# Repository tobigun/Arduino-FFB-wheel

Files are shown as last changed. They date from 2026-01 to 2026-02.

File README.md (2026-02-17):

# Customized Arduino-FFB-wheel for Guillemot Force Feedback Racing Wheel
## About this project
### Motivation
It gets more and more difficult to find working Windows 11 drivers for this wheel.

Even the old [Vista drivers](https://support.thrustmaster.com/en/product/ffdrw-en/) which worked fine for me some years ago only work with the iRacing FFB test program (WheelCheck.exe) anymore, but not with any of my games - they simply crash. I already replaced "System32/immpid.dll" with the one from "SysWOW64" and although this fixes the crashes I do not get any Force Feedback effects in games at all (the green effect LED on the Main PCB also does not blink).

There is also another old [driver on archive.org](https://archive.org/details/Guillemot-Thrustmaster-ForceFeedback-wheel-64bit-driver) which is supposed to work according to some forums. But even after disabling the Windows driver signature check the driver was marked as non-functional in the device manager and was not functional.

As a consequence I decided to reverse engineer the hardware and replace the Main PCB of the wheel with an Arduino Pro Micro board. This way it supports Force Feedback via USB HID and does not need any drivers at all.
The nice thing about this wheel is that the Motor Control PCB can be reused and only the Logic Board has to be replaced.

For the firmware I tried multiple projects, e.g.:
- [ranenbg/Arduino-FFB-wheel](https://github.com/ranenbg/Arduino-FFB-wheel)
- [vsulako/AFFBWheel](https://github.com/vsulako/AFFBWheel) (see my [unfinished fork here](https://github.com/tobigun/AFFBWheel))
- [YukMingLaw/ArduinoJoystickWithFFBLibrary](https://github.com/YukMingLaw/ArduinoJoystickWithFFBLibrary)

Arduino-FFB-wheel was the most complete, so this project was used as the foundation.

### Game Compatibility Matrix
|Game|Store|Status|
|----|----|---|
|Assetto Corsa|Steam|OK
|Assetto Corsa Competizione|Steam|OK
|DiRT Rally 2.0|Steam|OK|
|Forza Horizon 4|Steam|OK. Requires the [Steering Wheel HID Profile](#hid-profiles), otherwise wheel will not be detected.|
|Forza Horizon 5|Steam|OK. Requires the [Generic HID Profile](#hid-profiles), otherwise game will crash at start.|
|NFS Heat|Steam|Only Steering, no FFB effects|
|NFS Hot Pursuit Remastered|Steam|OK|
|NFS Most Wanted|Steam|OK. Seems to support vibrations only, as FFB effects are week.|
|NFS Undercover|Steam|OK|

### Firmware
This repo is a fork of Miloš Ranković's [Arduino-FFB-wheel](https://github.com/ranenbg/Arduino-FFB-wheel), customized for the Guillemot Force Feedback Racing Wheel. As none of the pre-compiled binaries of the original project were suitable for this wheel, this project provides a configuration for the hardware and some minor software adjustments.

**Hardware configuration:**
- Analog X-Axis
- Hat Switch
- PWM motor control in 0-50-100 mode (hardcoded, so no need to configure it via the config software)
- Matrix keypad with 12 buttons
- Usage of 5 analog axis:
  - X-Axis (wheel angle)
  - Throttle
  - Brake
  - 2x analog levers on the wheel
- Force Feedback (of course)

### Original PCBs
The wheel consists of five PCBs:

- Main PCB, i.e. the logic board with the I-Force 2.0 chip:<br>
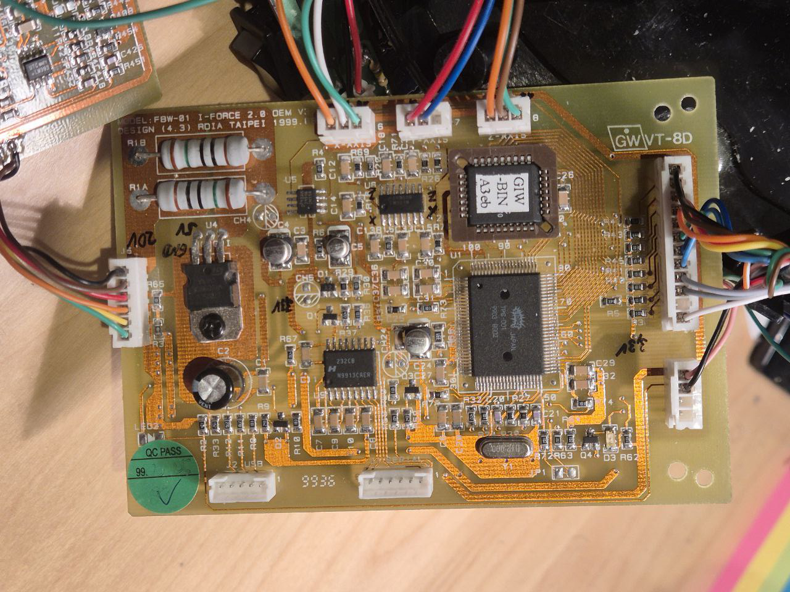
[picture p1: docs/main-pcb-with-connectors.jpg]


- Motor PCB (contains the PWM H-Bridge):<br>
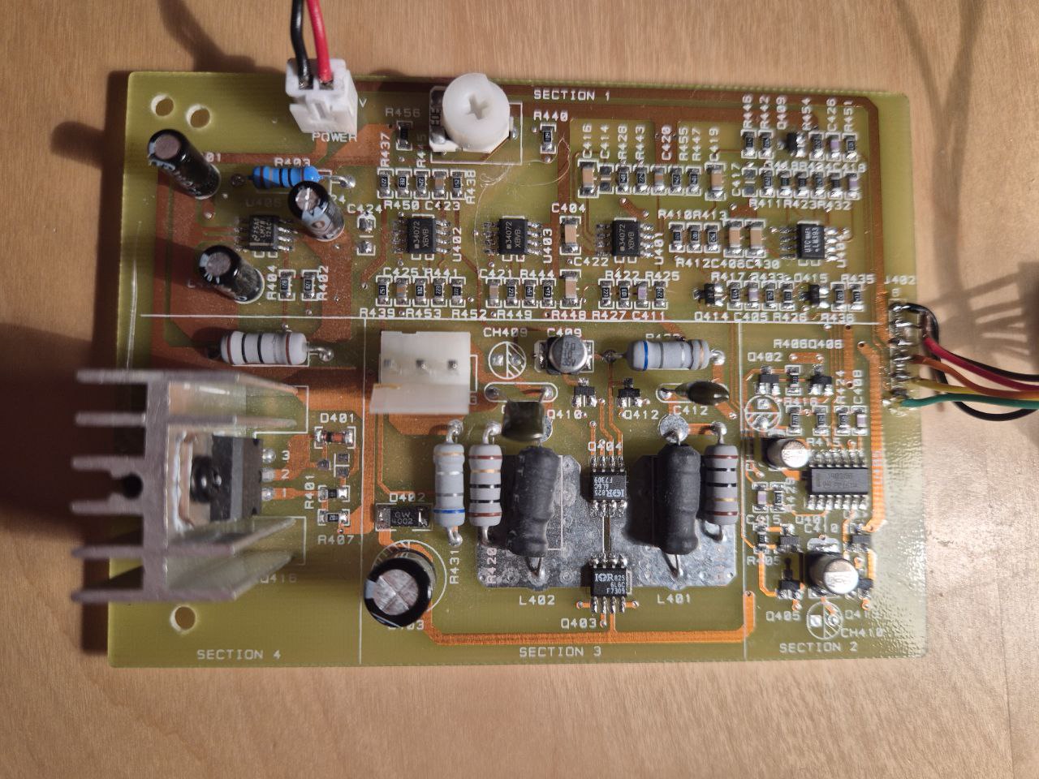
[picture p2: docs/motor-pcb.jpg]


- Front Button PCB:<br>
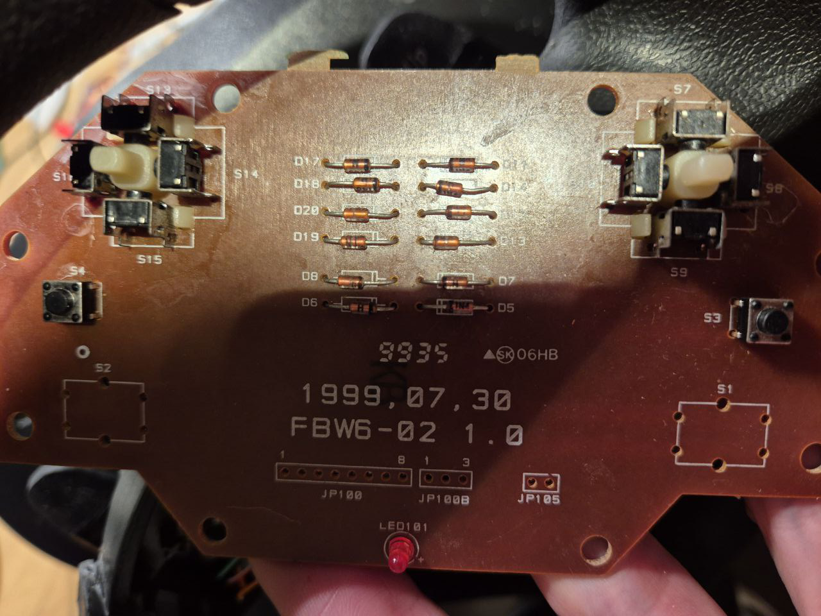
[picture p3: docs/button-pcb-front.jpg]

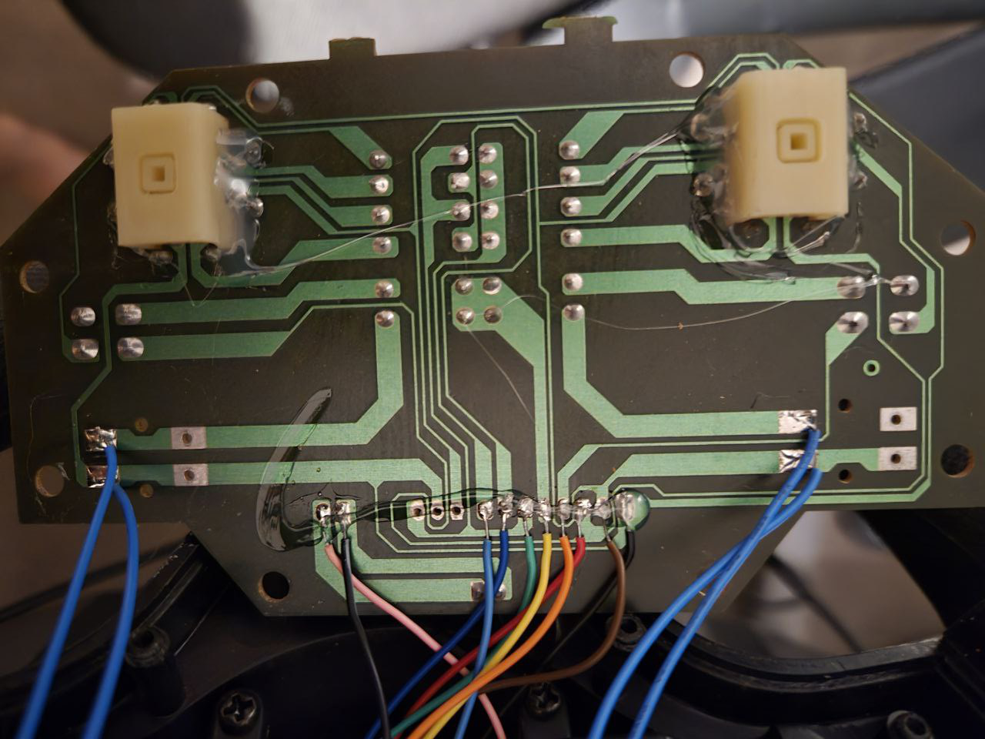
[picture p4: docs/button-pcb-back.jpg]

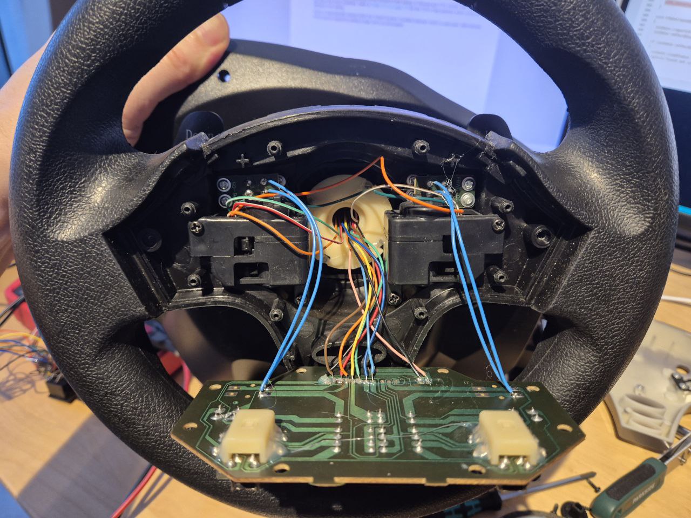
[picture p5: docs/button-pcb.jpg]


- Gear Shift PCB:<br>
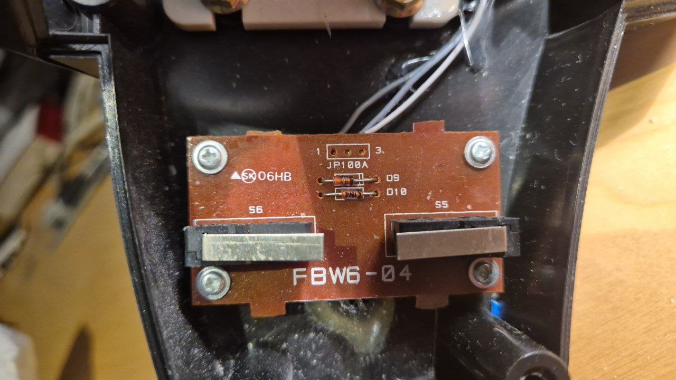
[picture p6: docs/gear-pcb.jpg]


- Power PCB (Note: already modified on the pictures). Contains power connector and switch, pedal connector and a digital switch (74HC4066). The 74HC4066 disables the two analog levers on the wheel when the pedals are connected.<br>
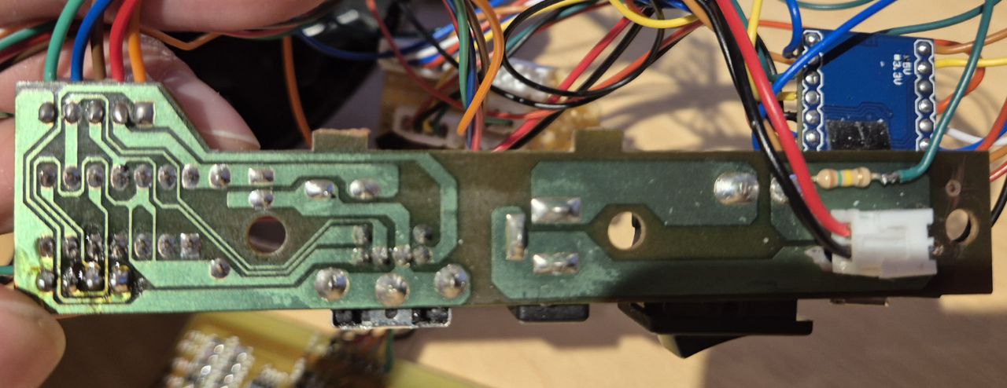
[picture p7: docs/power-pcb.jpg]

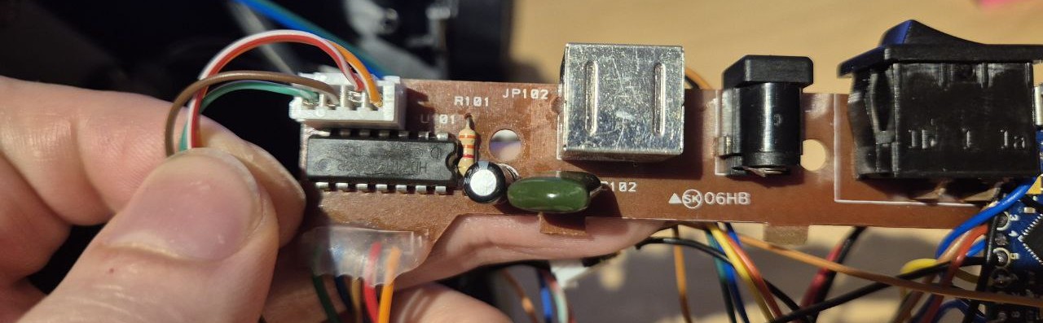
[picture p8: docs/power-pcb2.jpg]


All PCBs connected:
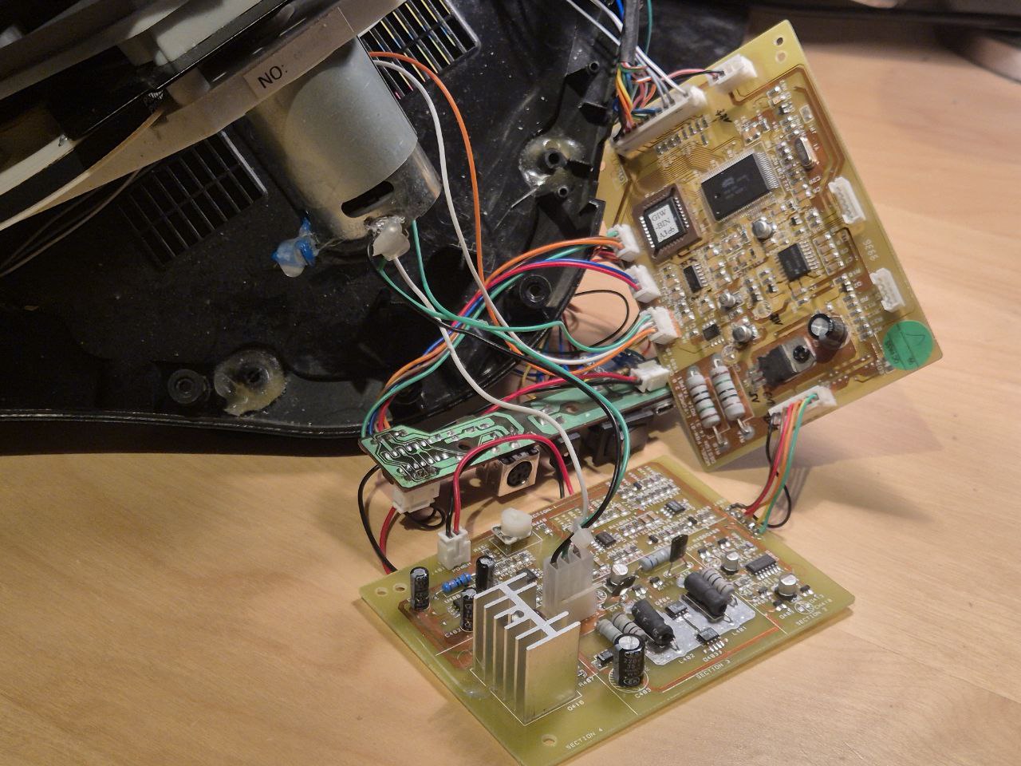
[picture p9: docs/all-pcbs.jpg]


### Arduino Main PCB
All of the original PCBs will be reused. The only PCB that will be replaced is the Main PCB. Instead an Arduino Pro Micro is used. I placed it on the Power PCB:
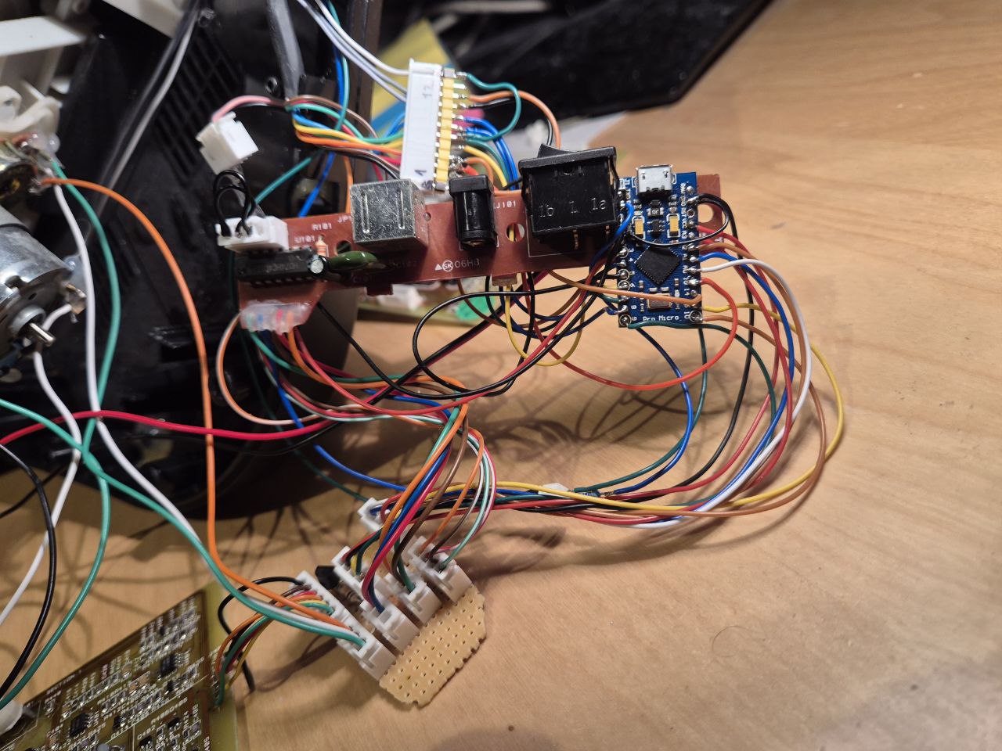
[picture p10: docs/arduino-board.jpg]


#### Wiring
Here is the overview of the connectors that are located on the Main PCB that now have to be connected to the Arduino board instead:
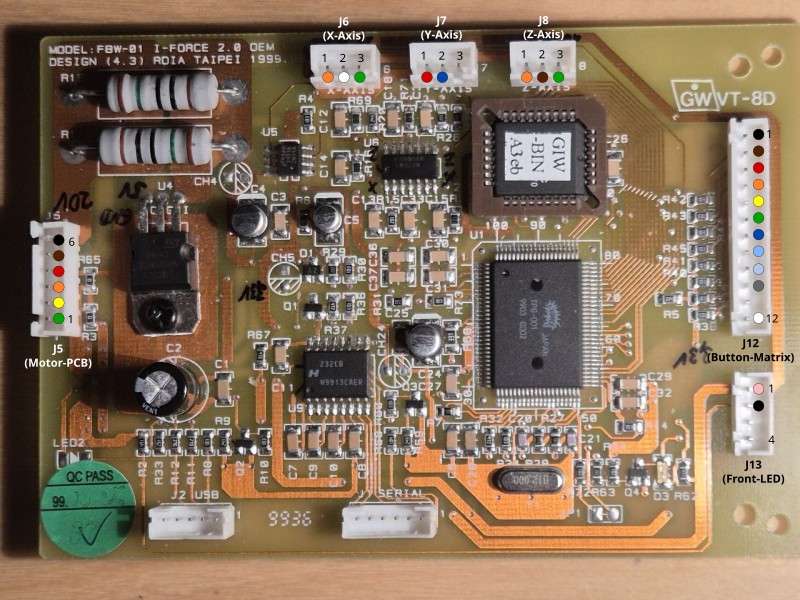
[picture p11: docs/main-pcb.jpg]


<table>
<tr><th colspan="3">Connector</th><th rowspan="2">Signal</th><th rowspan="2">Pin (ESP32-S3)</th><th rowspan="2">Pin (Pro Micro)</th><th rowspan="2">Comment</th></tr>
<tr><th>Name</th><th>Pin</th><th>Color</th></tr>

<tr><td rowspan="6">J5 (Motor PCB Connector)</td>
    <td>1</td><td style="background:green">green</td><td>Motor PWM</td><td>GP42</td><td>D9</td>
    <td rowspan="6">* Motor Enable switch must be connected to GP39/D10 via a BJT transistor to make sure that the motor is disabled when the microcontroller is powered down (i.e. not connected to USB).<br>
    This is necessary as the Motor PCB would erroneously interpret the missing PWM signal to apply maximum force. It would turn the wheel with full force in one direction and try to move it past the end stop. As this is not possible the motor gets quite hot after some minutes.
    <br>See schematic for more info.
    </td></tr>
<tr><td>2</td><td style="background:yellow">yellow</td><td>Motor Enable switch</td><td>[GP41]*</td><td>[D10]*</td></tr>
<tr><td>3</td><td style="background:orange">orange</td><td>GND</td><td colspan="2">GND</td></tr>
<tr><td>4</td><td style="background:red">red</td><td>GND</td><td colspan="2">GND</td></tr>
<tr><td>5</td><td style="background:brown">brown</td><td>GND</td><td colspan="2">GND</td></tr>
<tr><td>6</td><td style="background:black;color:white">black</td><td>+20V (from power supply)</td><td colspan="2">- (unused)</td></tr>

<tr><td rowspan="3">J6 (X-Axis Potentiometer)</td>
    <td>1</td><td style="background:orange">orange</td><td>VCC</td><td colspan="2">VCC</td><td rowspan="3"></td></tr>
<tr><td>2</td><td style="background:white">white</td><td>Analog X-Axis (0 .. VCC)</td><td>A0</td><td>A0</td></tr>
<tr><td>3</td><td style="background:green">green</td><td>GND</td><td colspan="2">GND</td></tr>

<tr><td rowspan="3">J7 (Y-Axis Potentiometer)</td>
    <td>1</td><td style="background:red">red</td><td>74HC4066 Supply Voltage</td><td colspan="2">VCC</td><td rowspan="3"></td></tr>
<tr><td>2</td><td style="background:blue;color:white">blue</td><td>Analog Y-Axis (0 .. VCC)</td><td>A1</td><td>A1</td></tr>
<tr><td>3</td><td style="background: repeating-linear-gradient(45deg,#eee,#eee 4px,#ccc 4px,#ccc 8px);">n.c.</td><td>-</td><td colspan="2">-</td></tr>

<tr><td rowspan="3">J8 (Z-Axis Potentiometer)</td>
    <td>1</td><td style="background:orange">orange</td><td>VCC</td><td colspan="2">VCC</td><td rowspan="3"></td></tr>
<tr><td>2</td><td style="background:brown">brown</td><td>Analog Z-Axis (0 .. VCC)</td><td>A3</td><td>A2</td></tr>
<tr><td>3</td><td style="background:green">green</td><td>GND</td><td colspan="2">GND</td></tr>

<tr><td rowspan="12">J12 (Button Matrix)</td>
    <td>1</td><td style="background:black;color:white">black</td><td>Matrix column 1</td><td>GP38</td><td>D5</td><td rowspan="12"></td></tr>
<tr><td>2</td><td style="background:brown">brown</td><td>Matrix column 2</td><td>GP37</td><td>D14</td></tr>
<tr><td>3</td><td style="background:red">red</td><td>Matrix column 3</td><td>GP36</td><td>D15</td></tr>
<tr><td>4</td><td style="background:orange">orange</td><td>Matrix column 4</td><td>GP35</td><td>D2</td></tr>
<tr><td>5</td><td style="background:yellow">yellow</td><td>Matrix row 1</td><td>GP17</td><td>D6</td></tr>
<tr><td>6</td><td style="background:green">green</td><td>Matrix row 2</td><td>GP33</td><td>D7</td></tr>
<tr><td>7</td><td style="background:blue;color:white">blue</td><td>Matrix row 3</td><td>GP18</td><td>D1 (TX0)</td></tr>
<tr><td>8</td><td style="background:#add8e6">light blue</td><td>Matrix row 4</td><td>GP34</td><td>D4</td></tr>
<tr><td>9</td><td style="background:#d3d3d3">light grey</td><td>Gear Shifter - Up (Matrix column 1)</td><td>GP38</td><td>D5</td></tr>
<tr><td>10</td><td style="background:grey">grey</td><td>Gear Shifter - Down (Matrix column 2)</td><td>GP37</td><td>D14</td></tr>
<tr><td>11</td><td style="background: repeating-linear-gradient(45deg,#eee,#eee 4px,#ccc 4px,#ccc 8px);">n.c.</td><td>-</td><td colspan="2">-</td></tr>
<tr><td>12</td><td style="background:white">white</td><td>Gear Shifter - Matrix row (Matrix row 2)</td><td>GP33</td><td>D7</td></tr>

<tr><td rowspan="4">J13 (Front LED)</td>
    <td>1</td><td style="background:#ff66cc">rose</td><td>LED Anode (+)</td><td>[GP40]*</td><td>[D3]*</td><td rowspan="4">* Connect LED's Anode via 820 Ohms resistor to pin.<br>See schematic for more info.</td></tr>
<tr><td>2</td><td style="background:black;color:white">black</td><td>LED Cathode (-)</td><td colspan="2">GND</td></tr>
<tr><td>3</td><td style="background: repeating-linear-gradient(45deg,#eee,#eee 4px,#ccc 4px,#ccc 8px);">n.c.</td><td>-</td><td colspan="2">-</td></tr>
<tr><td>4</td><td style="background: repeating-linear-gradient(45deg,#eee,#eee 4px,#ccc 4px,#ccc 8px);">n.c.</td><td>-</td><td colspan="2">-</td></tr>

<tr><td rowspan="4">JP101 (Analog Levers)<br>[Optional]</td>
    <td>1</td><td style="background:orange">orange</td><td>VCC</td><td colspan="2">VCC</td>
    <td rowspan="4">Wires can be unsoldered from connector JP101 of the power PCB and directly connected to the microcontroller.
    This way the pedals and levers can be used in parallel (5 instead of 3 axes). The Pins 2+3 on the JP101 connector on the power board should be pulled high then (i.e. connected to Pin 1).<br>See schematic for more info.</td></tr>
<tr><td>2</td><td style="background:red">red</td><td>Analog Axis - Lever left</td><td>A4</td><td>A3</td></tr>
<tr><td>3</td><td style="background:brown">brown</td><td>Analog Axis - Lever right</td><td>A5</td><td>A8</td></tr>
<tr><td>4</td><td style="background:green">green</td><td>GND</td><td colspan="2">GND</td></tr>

<tr><td rowspan="2">Blue Front LED<br>[Optional]</td>
    <td>A</td><td style="background:blue"></td><td>LED Anode (+)</td><td>[GP39]*</td><td>[D0]* (RX1)</td>
    <td rowspan="2">* Connect LED's Anode via 4.7 kOhms resistor to pin.<br>See schematic for more info.</td>
    </tr>
<tr><td>C</td><td style="background:black;color:white"></td><td>LED Cathode (-)</td><td colspan="2">GND</td></tr>

<tr><td rowspan="2">Green Front LED<br>[Optional]</td>
    <td>A</td><td style="background:green"></td><td>LED Anode (+)</td><td colspan="2">[+20V]*</td>
    <td rowspan="2">* Connect LED's Anode via 150 kOhms resistor to +20V.<br>See schematic for more info.</td>
    </tr>
<tr><td>C</td><td style="background:black;color:white"></td><td>LED Cathode (-)</td><td colspan="2">GND</td></tr>

<tr><td rowspan="2">Profile Switch<br>[Optional]</td>
    <td>1</td><td></td><td>Pin 1</td><td>GP7</td><td>D16</td>
    <td rowspan="2">For three pin switches: connect middle pin to D16 and any of the other two pins to GND.<br>
    </td></tr>
<tr><td>2</td><td style="background:black;color:white"></td><td>Pin 2</td><td colspan="2">GND</td></tr>
</table>

Make a little connector hub PCB to hold the motor switch transistor and  to connect all of the GND and VCC pins together. This way you can keep the existing connectors and you will still be able to reconnect them to the original Main PCB. But you can also cut the original connectors and solder the wires directly to the Arduino board.
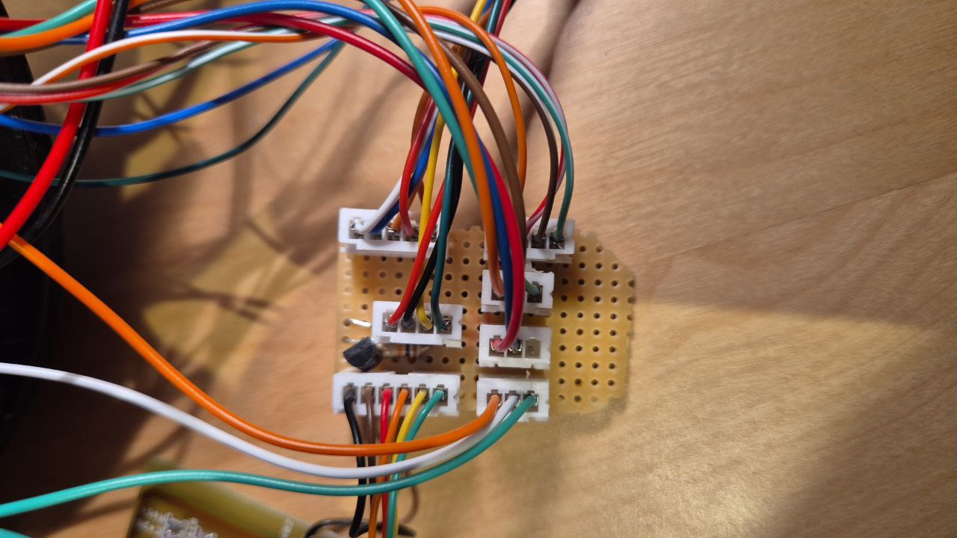
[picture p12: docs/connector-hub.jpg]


#### HID Profiles
A Profile Switch can be added to select between to HID profiles:
- Switch open: Generic Joystick with generic X/Y/Z/Rx/Rz Axes (default)
- Switch closed: Steering wheel with Steering/Brake/Accelerator/Rx/Rz Axes

Switching profiles is necessary as there is no unified way to detect a Driving Wheel on Windows.
- Some games only detect a driving wheel if a Steering-Wheel Axis is present in the USB HID descriptor (e.g. Forza Horizon 4).
  - It seems that mostly older DirectInput based games require this profile as DirectInput uses a heuristic to detect wheels based on the axes of the controller ([see Wine DirectInput Port](https://github.com/wine-mirror/wine/blob/master/dlls/dinput/joystick_hid.c)).
- Some games require a generic X-Axis and do not work (or crash) when a Steering-Wheel Axis is present.
  - For example, Forza Horizons 5 crashes if a Steering-Wheel Axis is found.

##### Registry Tweak for Generic Profile
Instead of adding a switch to change the HID profile, for some games (like Forza Horizon 4) the Generic Profile also works if the following Windows registry keys are added via `regedit`:
```
Computer\HKEY_CURRENT_USER\System\CurrentControlSet\Control\MediaProperties\PrivateProperties\Joystick\OEM\VID_1B4F&PID_9206
Computer\HKEY_LOCAL_MACHINE\System\CurrentControlSet\Control\MediaProperties\PrivateProperties\Joystick\OEM\VID_1B4F&PID_9206
```
Add or modify the following value/data pair in these keys:
|Name|Type|Data
|----|----|----
|OEMData|REG_BINARY|43 00 88 01 fe 00 00 00

This can be achieved by double clicking on the `FFB_misc_programs/wheel-oemdata-add.reg` file.
The entries can be removed again with the `wheel-oemdata-remove.reg` file.

The bits of OEMData are described [here](https://sourceforge.net/p/timidity/git/ci/master/tree/windrv/mmddk.h#l230) but do not seem to be that important, as long as it starts with `43`.

See [Steam Community article on Forza Horizon 4 by LeadMagnet](https://steamcommunity.com/sharedfiles/filedetails/?id=2909923087) for more info.

> [!IMPORTANT]
> Make sure that the registry entries are removed again for Forza Horizons 5, as this game crahes if the entries are present.

------------------

# Arduino-FFB-wheel
A stand-alone DirectInput USB device is recognized in Windows as a joystick with force feedback functionality, based on BRWheel by Fernando Igor in 2017.

Firmware features:
- supported Arduino boards: Leonardo, Micro, and ProMicro (ATmega32U4, 5V, 16MHz)
- 4 analog axis + 1 for an optical or magnetic encoder, 2 FFB axis (with multichannel PWM or DAC output)
- for 2 FFB axis mode - 2 magnetic encoders may be used (for X and Y axis)
- automatic or manual analog axis calibration
- up to 16 buttons by 4x4 matrix or via **[button box firmware](https://github.com/ranenbg/Arduino-FFB-wheel/tree/master/tx_rw_ferrari_458_wheel_emu_16buttons)** uploaded to Arduino Nano/Uno
- up to 24 buttons by 3x8bit shift register chips
- analog XY H-pattern shifter (configurable to 6 or 8 gears + reverse gear, XY axis invert, reverse gear button invert)
- fully supported 16bit FFB effects (custom force effect not implemented)
- envelope and conditional block effects, start delay, duration, deadband, and direction enable
- FFB calculation and axis/button update rate 500Hz (2ms period)
- many firmware options (external 12bit ADC/DAC, automatic/manual pedal calibration, z-index support/offset/reset, hat switch, button matrix, external shift register, hardware wheel re-center, xy analog H shifter, FFB on analog axis)
- RS232 serial interface for configuring many firmware settings (10ms period)
- fully adjustable FFB output in the form of 4-channel digital 16bit PWM or 2-channel analog 12bit DAC signals
- available PWM modes: PWM+-, PWM+dir, PWM0-50-100, RCM (if 2 FFB axis: 2CH PWM+-, 2CH PWM+dir, 2CH PWM0-50-100, 2CH RCM)
- available DAC modes: DAC+-, DAC+dir, DAC0-50-100 (if 2 FFB axis: 1CH DAC+-, 2CH DAC+dir, 2CH DAC0-50-100)
- load cell support for 24bit HX711 chip (for Y axis only)
- all firmware settings are stored in EEPROM (and automatically loaded at each Arduino powerup)
- original wheel control user interface **[Arduino FFB gui](https://github.com/ranenbg/Arduino-FFB-gui)** for an easy configuration and monitoring of all inputs/outputs 

Detailed documentation and more information about the firmware can be found in txt files inside the `docs/fw` folder.

# Firmware pinouts and wiring diagrams
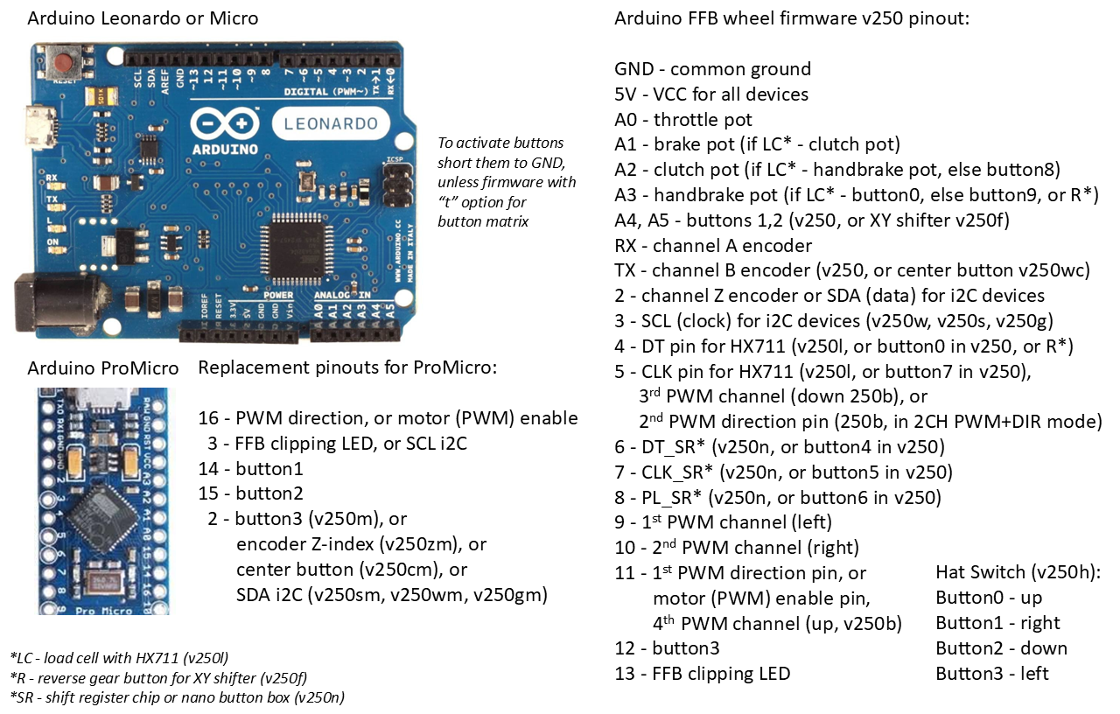
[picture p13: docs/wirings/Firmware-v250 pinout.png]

**Note:** some pin mappings in the image are outdated. Check the wiring table above for the correct ones.
## Optical encoder and LED wiring
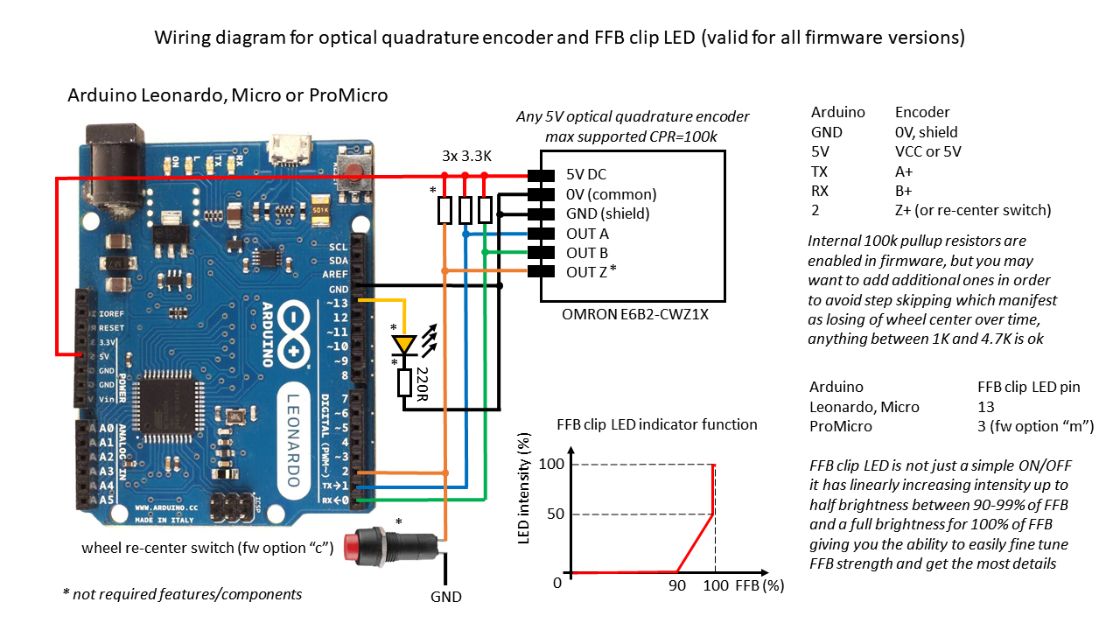
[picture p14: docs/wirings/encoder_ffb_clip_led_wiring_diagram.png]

## Button matrix pinouts
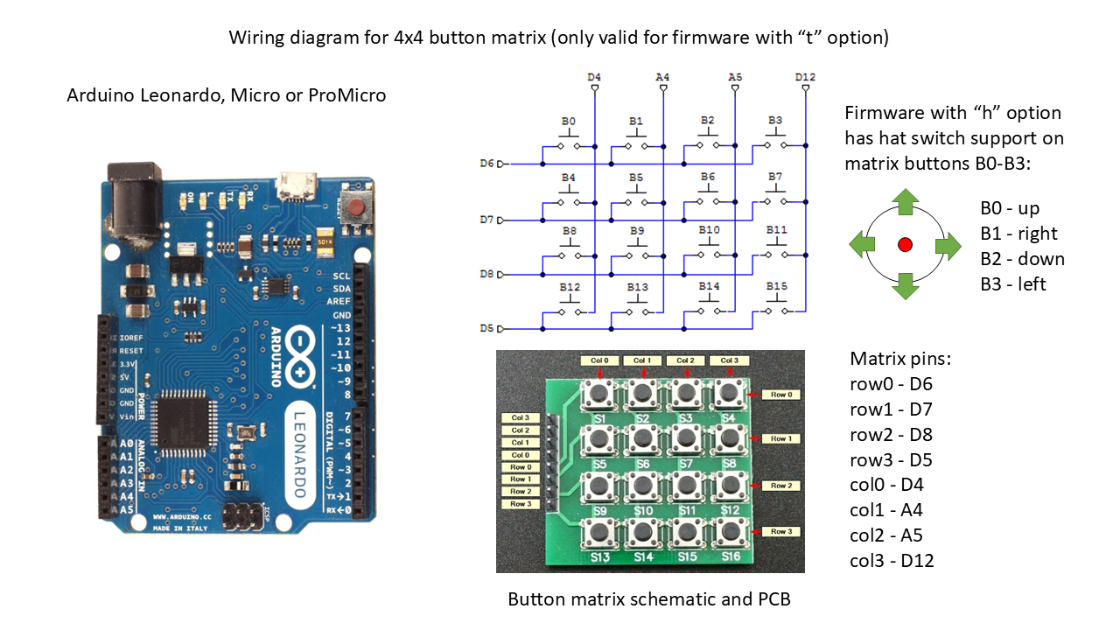
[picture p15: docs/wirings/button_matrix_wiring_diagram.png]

**Note:** the digital inputs for the matrix are not correct in the image. Check the wiring table above for the correct ones.

## Firmware upload procedure
You can use XLoader from the `misc_programs/XLoader` folder:
- set 57600baud, ATmega32U4 microcontroller and select desired HEX
- press the reset button on Arduino (or shortly connect the RST pin to GND)
- select the newly appeared COM port (Arduino in bootloader mode*) and press upload, you will only have a few seconds

*It is possible that some cheap Chinese clones of Arduino Leonardo, Micro, or ProMicro do not have a bootloader programmed. In that case you need to upload the original Arduino Leonardo bootloader first. You can find more details about it here: https://docs.arduino.cc/built-in-examples/arduino-isp/ArduinoISP

## How to compile the source
In order to compile the firmware yourself you may use Windows 11, you need to install Arduino IDE v2.3.6 and Arduino Boards v1.8.7. You must place the libraries (from the `libraries` folder) in your `.../documents/Arduino/Libraries` folder.

## Credits
- Miloš Ranković: [Arduino-FFB-wheel](https://github.com/ranenbg/Arduino-FFB-wheel)
- FFB HID and USB core for Arduino by: Peter Barrett
- BRWheel firmware by: Tero Loimuneva, Saku Kekkonen, Etienne Saint-Paul, and Fernando Igor
https://github.com/fernandoigor/BRWheel/tree/alphatest

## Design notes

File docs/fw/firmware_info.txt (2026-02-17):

Milos Rankovic, ranenbg@gmail.com
first created 21.11.2018.
last updated 02.08.2025.

This txt file contains full details about Arduino FFB wheel firmware capabilities and features:

Supported Arduino boards - Leonardo, Micro or ProMicro (5V, 16MHz clock)

firmware	PWM freq	PWM mode	PWM res		steering	brake		throttle	clutch		handbrake	buttons		HAT Switch	XYshifter

ver250		8KHz*		PWM+-*		2047*		16bit	        16bit(LC,a,s)	12bit(a,s)	12bit(a,s)	12bit(a,s)	24(16)		1		10bit

*fully configurable through RS232 or Wheel control v2.6.5

LC - load cell module HX711 24bit, 1 sample no-averaging, limited by Microsoft FFB driver to 16bits (0-65535)
a - Arduino analog input, 10bit (0-1023)
s - ADS1015, external ADC, 12bit (0-4095)
**HID supports total of 28 buttons, but only 24 buttons are visible, because 4 buttons are reserved for D-pad (HAT switch) 
firmware is compatible with any Thrustmaster wheel rim at 3.3v
be careful! 5V to 3.3V logic level converter is needed from Arduino wheel base board to Thrustmaster wheel rim
first 6 buttons are reserved for recognition of Thrustmaster wheel rims
Leonardo, Micro or ProMicro - up to 8 buttons are available on the main Arduino board (may be less depending on firmware options)
With external Arduino Nano board acting as a button box, up to 16 buttons can be used (button box firmware included in a separate *.ino file)
Only with external 8bit shift register chips 24 buttons can be used (if 3 are stacked together)

Axis readout adjustment (LC, a, s) and auto calibration (on/off) - requires recompiling

Available sensors on X-axis (for steering, tied to FFB axis):
[1] Optical encoder - quadrature readout of two channels, 1k-10k pullup resistors optional, available CPR range in firmware depends on selected deg of rotation (DOR), the limitation is CPR*DOR/360 <= 600k
[2] Magnetic encoder - 12bit i2C AS5600 (default CPR=4096, set to full precision and 2.2ms response time, multiturn detection supported)
[3] Potentiometer - any linear pot 10k-100k Ohm

USB poll. rate	FFB calc. rate	RS232 refresh	RS232 baud rate		axis update rate	LC update rate		buttons,D-pad,XY_shifter update rate

500Hz (2ms)	500Hz (2ms)	100Hz (10ms)	115200bit/s		500Hz (2ms)		80Hz (12.5ms)		500Hz (2ms)

Supported FFB effects: constant force, ramp, spring, damper, inertia, friction, sine, triangle, square, sawtoothup, sawtoothdown

FFB mics: all effects are calculated with 32bit precision and scaled down to 16bit in HID; realistically calculated damper, inertia and friction; fully working periodic effects;
fully implemented condition and envelope block effects, effect duration, start delay, direction for 2 axis FFB, *2channel PWM/DAC output for xFFB and yFFB

*FFB effects that support 2 FFB axis are: constant force, sine and spring

Internal FFB effects: auto centering spring, damper, inertia, friction and end stop spring (can be turned on/off through serial interface)

Firmware features: RS232 interface for adjusting all FFB parameters, LC brake pressure, pedal autocalibration, minimal PWM value, rotation angle, recenter wheel,
recalibrate wheel, recalibrate pedals, wheel version info reporting, turning various desktop effects on/off, turn on/off real-time FFB signal monitor, save FFB config to EEPROM,
adjustment of encoder CPR, fully adjustable PWM settings that are stored in EEPROM, FFB clip LED indicator (lights up gradually from last 10% of FFB signal level),
4x4 button matrix, CPR range up to 100k, wheel angle used as metric for spring, damper, inertia and friction effects, encoder z-index reset, PWM motor enable pin feature, single or double magnetic encoder support, 2 FFB axis and 4 channel PWM or 2 channel DAC output, 3x8bit shift register chip support for 24 buttons

Wheel control GUI: made from scratch in Processing 3.5.4, visualizes all axis and buttons including serial commands sent and received from Arduino, full adjustment of FFB effect gains,
FFB signal monitor graph, load/save last settings from EEPROM, recenter wheel, recalibrate pedals, encoder CPR adjustment, PWM adjustment, COM port CFG via dialog,
Axis colors CFG txt, storing/loading FFB profiles to/from PC, autodetection of firmware version, XY analog shifter support, manual pedal axis calibration, PWM0.50.100 mode, hardware button wheel re-center, RCM PWM mode, Z-index reset button, FFB axis selector, XY shifter advanced config buttons, advanced info startup diagnostics, encoder type indicator, detection of available wheel buttons, 2-axis FFB joystick representation instead of a wheel, new CP5 blue FFB sliders, re-sizeable GUI window, latest version is v2.6.5

FFB output options (requires recompiling):
[1] digital: 4 channel fully configurable PWM settings - PWM frequency (tied to PWM resolution), PWM types (phase correct or fast pwm), 1CH PWM modes (PWM+-, PWM+DIR, PWM0-50-100, RCM), 2CH PWM modes (2CH PWM+-, 2CH PWM+DIR, 2CH PWM0-50-100, 2CH RCM - not used), changes of PWM settings require restarting Arduino
[2] analog: 2 external i2C 12bit MCP4725 DAC's, 1CH DAC modes (DAC+-, DAC+DIR, DAC0-50-100), 2CH DAC modes (1CH DAC+- (xFFB), 2CH DAC+DIR, 2CH DAC0-50-100), changes of DAC settings do not require restarting Arduino

          PWM freq  index: 0,   , 1    , 2    , 3   , 4   , 5     , 6     , 7    , 8    , 9    , 10   , 11   , 12
Available PWM frequencies: 40kHz, 20kHz, 16kHz, 8kHz, 4kHz, 3.2kHz, 1.6kHz, 976Hz, 800Hz, 488Hz, 533Hz, 400Hz, 244Hz
Available PWM resolutions: 400  , 800  , 1000 , 2000, 4000, 5000  , 10000 , 16383, 20000, 32767, 30000, 40000, 65535 (for fast pwm - PWM type)
                           200  , 400  , 500  , 1000, 2000, 2500  ,  5000 ,  8191, 10000, 16383, 15000, 20000, 32767 (for phase correct - PWM type)
          PWM freq  index: 0,   , 1    , 2    , 3   , 4    , 5    , 6    , 7     , 8    , 9    , 10   , 11   , 12
Available RCM frequencies: na   , na   , na   , na  , 500Hz, 400Hz, 200Hz, 122Hz , 100Hz, 61Hz , 67Hz , 50Hz , 31Hz (for both fast pwm and phase correct types)
na-not available

Usage of PWM modes: PWM+- (H-bridge usage), PWM+DIR (BLDC or AC servo drive usage), PWM0-50-100 (various 3 phase BLDC motor drivers, use fast pwm PWM type with this mode, 0-full left force, 50-zero force, 100-full left force), RCM mode (RC servo driver and some 3 phase brushless drivers usage, 1.0ms pulse width - full left force, 1.5ms pulse width - zero force, 2.0ms pulse width - full right force)

Usage of DAC modes: DAC+- mode requires using a differential opamp in order to provide +-10V analog output, 1CH and 2CH DAC0-50-100 modes have zero force represented at half of DAC range 2.5V, 0V is full left/down and 5V is full right/up (usage of differential opamp is recommended if +- voltage output is desired)

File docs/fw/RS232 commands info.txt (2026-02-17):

Milos Rankovic, ranenbg@gmail.com
first created 25.03.2020.
last update 19.03.2024.

This txt file contains a list of all available RS232 serial interface commands implemented in my latest Arduino FFB wheel firmware version fw-v250 (you can use this info to make your own control GUI)

Arduino boards are also recognized as a virtual serial communication device (COM port) through which we can send/receive commands to/from the ATmega32U4 microcontroller

RS232,   commands are not case sensitive (in this manual capital letters are used only as an example)
         some commands do not have any parameter following a command char, but if they do, a range of available input values is given
         all commands must be terminated with CR: carriage return - char(13)
         upon receiving valid command Arduino terminates all responses with CR+LF: carriage return - char(13) and line feed - char(10)
         some commands have response and some don't (in this txt file, null means no serial response from Arduino)
         most commands can apply changes right away, but some require Arduino restart (for PWM settings - reconfiguration of internal timer registers is necessary)
         if Arduino restart is needed, do not send any additional commands before restart
         firmware will check if any serial command is received every 10ms (100Hz refresh rate)
         Arduino response time is therefore maximally 10ms, but typically is around (2-5)ms
         at each Arduino powerup firmware will automatically load and configure all settings from EEPROM (for load cell - it takes additional 2s for completing tare zeroing)
         FFB clip LED will quickly blink 3 times to indicate that everything is loaded, configured and ready to use

versions, I have put some logic in firmware naming, so here is some basic explanation (if you plan to upgrade firmware, please respect this, only up to fw-v24X):
         fw-vXX,  two digits only are a test versions of new firmware features (not used anymore)
         fw-vXX0, three digits ending with 0 - the basic firmware with no external devices support, except for optical/magnetic encoder (has PWM signal as FFB output)
         fw-vXX1, three digits ending with 1 - adds support for external button box
         fw-vXX2, three digits ending with 2 - adds support for both external button box and load cell
         fw-vXX3, three digits ending with 3 - adds support for external button box, load cell and two external 12bit DAC - MCP4725 (has analog signal as FFB output)

versions from fw-v250, I've changed firmware naming logic such that all 3 digits in the name now represent firmware version only (everything else is an option, see bellow)

options, firmware version string may include some letters after digits, their meaning is:
         a - pedal autocalibration enabled (if no a, then manual calibration is enabled)
         b - 2 FFB axis support with physical output (4 channel digital PWM or 2 channel analog DAC outputs available)
	 w - magnetic encoder AS5600 support
         d - no optical encoder support
         z - optical encoder with z-index support
         h - enabled Hat Switch (uses first 4 buttons from button box)
         s - enabled external 12bit ADC for analog inputs (ADS1015 i2C)
         t - enabled 4x4 button matrix
         f - enabled XY analog H-pattern shifter
         i - enabled averaging of analog inputs
	 e - support for two additional digital buttons (clutch and handbrake axis will be unavailable)
	 x - enables the option to select to which (analog) axis is FFB tied to
         r - support for external shift register chips for 24 buttons (3x SN74ALS166 wired in series)
         n - support for external button box for 16 buttons via Arduino nano (with my button box firmware)
         l - support HX711 chip for load cell
         g - support for external 12bit DAC to be used for analog FFB output (2x MCP4725 i2C)
	 p - no EEPROM support for loading/saving firmware settings (firmware defaults are loaded at each startup)
         m - replacement pinouts for ProMicro (for FFB clipping LED, buttons 3 and 4, PWM direction pin)

[1] all wheel parameters read out
received numbers are: wheel rotation angle, general, damper, friction, constant, 
periodic, spring, inertia, auto center spring and end stop spring effect gains,
min torque PWM, brake pressure, desktop effects byte, total PWM steps (resolution), encoder CPR and PWM configuration byte
command		example response
U		1080 100 50 50 100 100 100 50 70 0 0 45 1 500 2400 9

[2] show firmware version
command		example response
V		fw-v240x

[3] show states for encoder
0 - not calibrated or no z-index found (normal for encoders without z-channel)
1 - calibrated or z-index found
2 - calibration error
command		example response
S		1			

[4] re-calibrate wheel
this feature has two modes of operation depending on firmware option "z"
(a)for firmware without "z" option, this procedure will try to rotate wheel to the right until a mechanical end stop is detected
do not use this command if you do not have a mechanical limits for wheel rotation installed (should use center command instead)
(b)for firmware with "z" option, this procedure will rotate the wheel until a z-index pulse from encoder is detected
at this position of z-index, a 0deg value will be assigned to the wheel (this may not be a real wheel zero angle)
if a wheel is not centered at this position (99% chance), return the wheel by hand to the center, then send "center" command, then send "save" command to save new z-index offset value
this procedure will store the z-index pulse angle offset in EEPROM 
on next Arduino powerup as soon as z-index is detected, the firmware will automatically apply the angle correction using the offset loaded from EEPROM
note that z-index angle offset will change if you re-mount your encoder, as you are not able to put it back to the exact same angle mechanically
command		example response
R		null

[5] adjust load cell brake pressure calibration factor (valid for fw-vXX2 only, for all other it becomes a *PWM balance slider)
sent and received number is only a relative value
each load cell will have a different max force
value of 4 will give 1:1 reading from HX711 24bit ADC chip
*PWM balance slider - you can use it to compensate for example if your motor has a stronger pull in one direction (128-center, equal pull in both directions)
value	leftPWM(%)	rightPWM (%)
0	100    		50
128	100		100
255	50		100
command		example response	range
B 45		1			1-255

[6] re-calibrate pedals
will reset pedal axis auto-calibration
if load cell is used for brake it will not affect its calibration factor and will only reset throttle and clutch
if no load cell is used reset will be done for brake axis as well
command		example response	range
P		1			null

[7] optical encoder CPR (PPR) adjustment
sent and received number is CPR - counts per revolution of encoder shaft (valid for optical, magnetic encoders and pots)
encoders usualy have specified PPR - pulses per revolution
CPR = 4 * PPR * X
X=1 if encoder is directly mounted to the wheel rim, otherwise it is a gear ratio between encoder and wheel shafts
if a pot is used for X-axis then CPR is tied to resolution of that analog input (Arduino 10bit 1024, with averaging 4096, or with ADS1105 in single ended readout 2048)
command		example response	range
O 2400		1			4-600000

[8] re-center wheel
use this command to reset 0deg position of your wheel rim (after you manually centering the wheel)
this will be required each time Arduino is powered on or reset, but it's very quick and easy to do
for HEX firmware with "z" option enabled, it will set z-index offset in the units of encoder CPR
command		example response	range
C		1			null

[9] reset encoder Z-index
use this command to set the Z-index encoder offset value to 0
after using this command you can move the wheel to a new position and press the center, than press save button
command		example response	range
Z		1			null

[10] adjust wheel rotation angle 
sent and received number is in degrees (lock-to-lock)
command		example response	range
G 900		1			30-1800

[11] adjust desktop effects
byte, bit0-autocentering spring, bit1-damper, bit2-inertia, bit3-friction, bit4-ffb monitor, bits5,7-are index of FFB axis selection (bit5 is LSB for index, 0 means X-axis)
bit0 - is LSB (lowest significant bit)
sent and received number is a decimal equivalent (form) of this byte
command		example response	range
E 1		1			0-31

[12] adjust PWM/DAC settings - only requires Arduino restart to apply PWM changes (press reset button, or just re-plug Arduino to USB port)
byte, bit0-phase correct (or fast pwm), bit1-dir enabled (or pwm+-), bits 2-5 are frequency select, bits6-pwm0-50-100 mode enable, bit7 is unused
PWM0-50-100 mode selection is done by setting bit1 LOW and bit6 HIGH
RCM mode selection is done by setting both bit1 and bit6 HIGH (please note that not all frequencies are available, see firmware_info.txt for more details)

bit0 pwm_type
0    fast pwm
1    phase correct

bit1 bit6 pwm_mode	pwm_mode2 (2-ffb axis)
0    0    pwm+-		2ch pwm+-
0    1    pwm0.50.100   2ch pwm0.50.100
1    0    pwm+dir       2ch pwm+dir
1    1    rcm           2ch rcm (not used)

IMPOPRTANT NOTE: if USE_MCP4725 is uncommented in Config.h then configuration byte has the following interpretation
bits 0-4 unused, bits 5,6 dac mode (see bellow), bit7 dac output (enable/disable)

bit7 dac_out
0    disabled (set to 0V or 2.5V depending on dac mode)
1    enabled

bit6 bit5 dac_mode     dac_mode2 (2-ffb axis)
0    0	  dac+-        1ch dac+- (xFFB)
0    1    dac0-50-100  2ch dac0-50-100
1    0    dac+dir      2ch dac+dir
1    1    none	       none

for available frequency selection see firmware info.txt
sent number is a decimal equivalent (form) of this byte
received number is PWM resolution (max number of PWM steps, for given PWM frequency and PWM type)
the settings will be stored in EEPROM right away (no additional saving is necessary with command A)
command		example response	range
W 5		400			0-255

[13] Save command - store firmware settings in EEPROM (stores everything except for PWM settings)
command		example response
A		1

[14] adjust FFB general (overall effects) gain
unit for sent and received number is %
command		example response	range
FG 100		1			0-200

[15] adjust FFB constant force effect gain
command		example response	range
FC 100		1			0-200

[16] adjust FFB damper effect gain
command		example response	range
FD 100		1			0-200

[17] adjust FFB friction effect gain
command		example response	range
FF 100		1			0-200

[18] adjust FFB periodic effect gain (affects sine, triangle, square, sawtoothup and sawtoothdown effects only) 
command		example response	range
FS 100		1			0-200

[19] adjust FFB spring effect gain
command		example response	range
FM 100		1			0-200

[20] adjust FFB inertia effect gain
command		example response	range
FI 100		1			0-200

[21] adjust FFB auto-centering spring effect gain
command		example response	range
FA 100		1			0-200

[22] adjust FFB end stop spring effect gain
command		example response	range
FB 100		1			0-200

[23] adjust minimal PWM signal level
unit for received number is x0.1%
range corresponds to (0.0-20.0)% of max PWM value
command		example response	range
FJ 100		1			0-200

[24] XY analog shifter calibration "a" limit
sets the X pos limit between 1st-2nd and 3rd-4th gear
command		example response	range
HA 255		1			0-1023

[25] XY analog shifter calibration "b" limit
sets the X pos limit between 3rd-4th and 5th-6th gear
command		example response	range
HB 511		1			0-1023

[26] XY analog shifter calibration "c" limit
sets the X pos limit between 5th-6th and 7th-8th gear
command		example response	range
HC 767		1			0-1023

[27] XY analog shifter calibration "d" limit
sets the Y pos limit between gears 1,3,5,7 and neutral
command		example response	range
HD 255		1			0-1023

[28] XY analog shifter calibration "e" limit
sets the Y pos limit between neutral and gears 2,4,6,8
command		example response	range
HE 511		1			0-1023

[29] XY analog shifter gear configuration byte
advanced configuration allows to adjust how shifter operates 
input is a decimal representation of a byte where
bit0=1: reverse gear button inverted (for Logitech G25/G27/G29/G923 H-shifters)
bit1=1: 8 gear mode (rev gear in 8th+rev button), otherwise it's in 6th+rev button
bit2=1: X-axis inverted
bit3=1: Y-axis inverted
command		example response	range
HF 2		1			0-255

[30] XY analog shifter calibration and config readout
returns shifter config byte and limits a, b, c, d, e
command		example response	range
HG		0 255 511 767 255 511	null

[31] XY analog shifter position readout
returns current h-shifter X and Y position
command		example response	range
HR		123 456			null

[32] manual pedal axis calibration "a" limit
sets the minimal calibration value for brake pedal
command		example response	range
YA		1			0-4095

[33] manual pedal axis calibration "b" limit
sets the maximal calibration value for brake pedal
command		example response	range
YB		1			0-4095

[34] manual pedal axis calibration "c" limit
sets the minimal calibration value for accelerator pedal
command		example response	range
YC		1			0-4095

[35] manual pedal axis calibration "d" limit
sets the maximal calibration value for accelerator pedal
command		example response	range
YD		1			0-4095

[36] manual pedal axis calibration "e" limit
sets the minimal calibration value for clutch pedal
command		example response	range
YE		1			0-4095

[37] manual pedal axis calibration "f" limit
sets the maximal calibration value for clutch pedal
command		example response	range
YF		1			0-4095

[38] manual pedal axis calibration "g" limit
sets the minimal calibration value for handbrake pedal
command		example response	range
YG		1			0-4095

[39] manual pedal axis calibration "h" limit
sets the maximal calibration value for handbrake pedal
command		example response	range
YH		1			0-4095

[40] manual pedal axis calibration readout
returns pedal axis calibration limit values a, b, c, d, e, f, g, h
note that depending on firmware options these limits have different ranges
range	fw-option
1023	all (except "s" and "i")	
2047	"s"
4095	"i"
command		example response		range
YR		0 4095 0 4095 0 4095 0 4095	null

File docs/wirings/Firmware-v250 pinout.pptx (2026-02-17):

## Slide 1

Arduino Leonardo or Micro

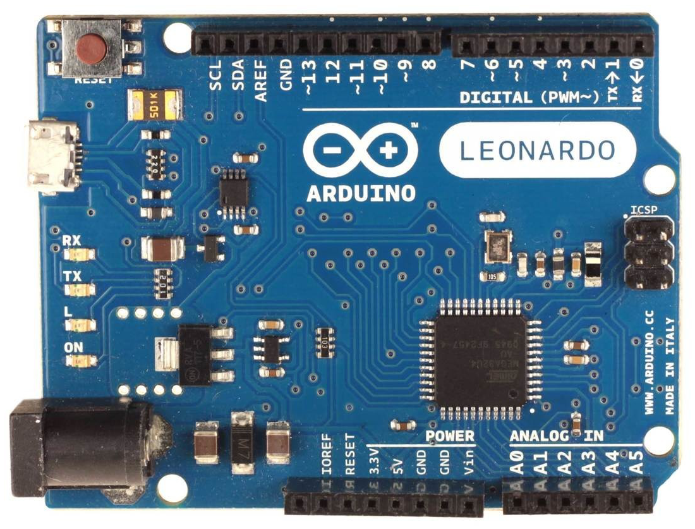
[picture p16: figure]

Replacement pinouts for ProMicro:
16 - PWM direction, or motor (PWM) enable
3 - FFB clipping LED, or SCL i2C
14 - button1
15 - button2
2 - button3 (v250m), or
encoder Z-index (v250zm), or
center button (v250cm), or
SDA i2C (v250sm, v250wm, v250gm)

Arduino FFB wheel firmware v250 pinout:
GND - common ground
5V - VCC for all devices
A0 - throttle pot
A1 - brake pot (if LC* - clutch pot)
A2 - clutch pot (if LC* - handbrake pot, else button8)
A3 - handbrake pot (if LC* - button0, else button9, or R*)
A4, A5 - buttons 1,2 (v250, or XY shifter v250f)
RX - channel A encoder
TX - channel B encoder (v250, or center button v250wc)
2 - channel Z encoder or SDA (data) for i2C devices
3 - SCL (clock) for i2C devices (v250w, v250s, v250g)
4 - DT pin for HX711 (v250l, or button0 in v250, or R*)
5 - CLK pin for HX711 (v250l, or button7 in v250),
3rd PWM channel (down 250b), or
2nd PWM direction pin (250b, in 2CH PWM+DIR mode)
6 - DT_SR* (v250n, or button4 in v250)
7 - CLK_SR* (v250n, or button5 in v250)
8 - PL_SR* (v250n, or button6 in v250)
9 - 1st PWM channel (left)
10 - 2nd PWM channel (right)
11 - 1st PWM direction pin, or
motor (PWM) enable pin,
4th PWM channel (up, v250b)
12 - button3
13 - FFB clipping LED

To activate buttons
short them to GND,
unless firmware with
“t” option for
button matrix

Arduino ProMicro

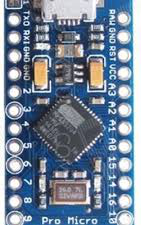
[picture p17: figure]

Hat Switch (v250h):
Button0 - up
Button1 - right
Button2 - down
Button3 - left

*LC - load cell with HX711 (v250l)
*R - reverse gear button for XY shifter (v250f)
*SR - shift register chip or nano button box (v250n)

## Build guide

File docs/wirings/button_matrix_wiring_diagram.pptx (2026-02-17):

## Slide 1

Wiring diagram for 4x4 button matrix (only valid for firmware with “t” option)

Arduino Leonardo, Micro or ProMicro

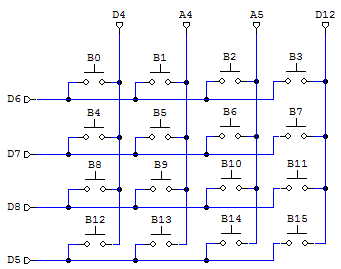
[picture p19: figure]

Firmware with “h” option
has hat switch support on
matrix buttons B0-B3:

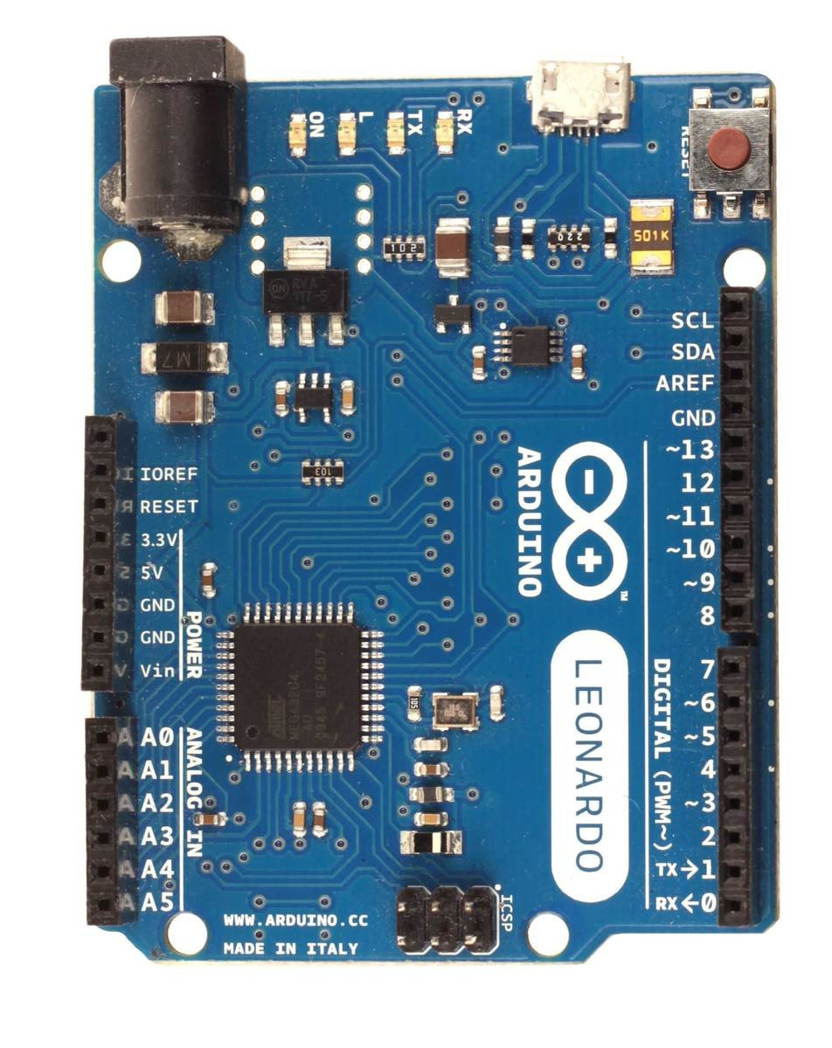
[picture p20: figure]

B0 - up
B1 - right
B2 - down
B3 - left

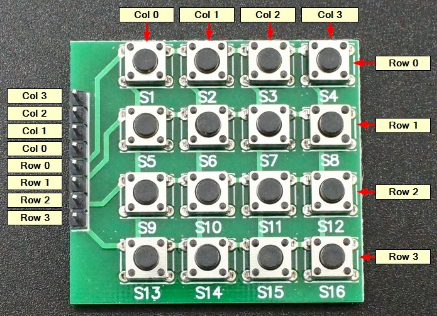
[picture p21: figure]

Button matrix schematic and PCB

Matrix pins:
row0 - D6
row1 - D7
row2 - D8
row3 - D5
col0 - D4
col1 - A4
col2 - A5
col3 - D12

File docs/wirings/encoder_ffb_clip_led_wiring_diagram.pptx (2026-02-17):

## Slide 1

Wiring diagram for optical quadrature encoder and FFB clip LED (valid for all firmware versions)

Arduino Leonardo, Micro or ProMicro

Any 5V optical quadrature encoder
max supported CPR=100k

5V DC
0V (common)
GND (shield)
OUT A
OUT B
OUT Z

OMRON E6B2-CWZ1X

Arduino Encoder
GND 0V, shield
5V VCC or 5V
TX A+
RX B+
2 Z+ (or re-center switch)

Internal 100k pullup resistors are
enabled in firmware, but you may
want to add additional ones in order
to avoid step skipping which manifest
as losing of wheel center over time,
anything between 1K and 4.7K is ok

Arduino FFB clip LED pin
Leonardo, Micro 13
ProMicro 3 (fw option “m”)
FFB clip LED is not just a simple ON/OFF
it has linearly increasing intensity up to
half brightness between 90-99% of FFB
and a full brightness for 100% of FFB
giving you the ability to easily fine tune
FFB strength and get the most details

3x 3.3K

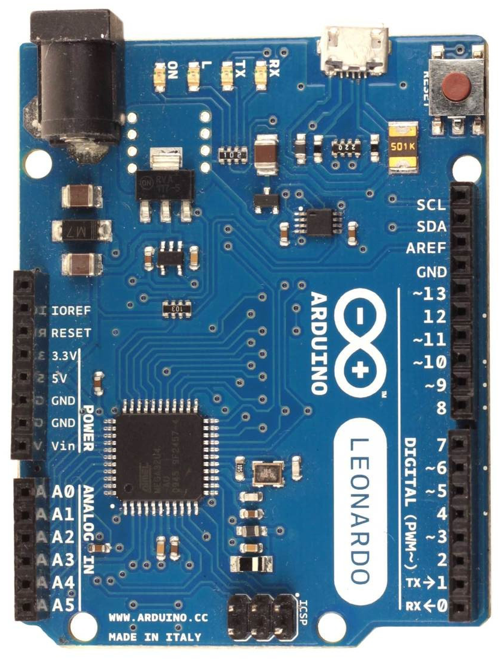
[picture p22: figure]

*

*

*

*

220R

FFB clip LED indicator function

100

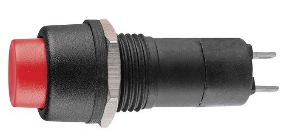
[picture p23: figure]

*

LED intensity (%)

50

wheel re-center switch (fw option “c”)

0

90

100

FFB (%)

* not required features/components

GND

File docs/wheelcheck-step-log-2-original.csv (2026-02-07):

force | startX | endX | deltaX | deltaXDeg
0 | 0 | 0 | 0 | 0
200 | -566 | -273 | 293 | 13.183594
400 | -351 | 78 | 429 | 19.335938
600 | 19 | -136 | -155 | -7.031250
800 | 156 | 78 | -78 | -3.515625
1000 | -351 | -351 | 0 | 0.000000
1200 | -273 | -195 | 78 | 3.515625
1400 | -58 | 78 | 136 | 6.152344
1600 | -273 | -488 | -215 | -9.667969
1800 | -195 | -136 | 59 | 2.636719
2000 | -195 | 78 | 273 | 12.304688
2200 | 156 | 19 | -137 | -6.152344
2400 | -58 | -195 | -137 | -6.152344
2600 | -273 | -273 | 0 | 0.000000
2800 | -136 | -136 | 0 | 0.000000
3000 | -195 | -195 | 0 | 0.000000
3200 | -58 | -351 | -293 | -13.183594
3400 | -136 | -351 | -215 | -9.667969
3600 | 19 | -136 | -155 | -7.031250
3800 | 19 | 507 | 488 | 21.972656
4000 | 10000 | 10000 | 0 | 0.000000
4200 | -3769 | 2031 | 5800 | 261.035156
4400 | 2851 | 3359 | 508 | 22.851563
4600 | -3515 | 3867 | 7382 | 332.226563
4800 | 3476 | 5253 | 1777 | 79.980469
5000 | -1757 | 6503 | 8260 | 371.777344
5200 | -2070 | 7011 | 9081 | 408.691406
5400 | -1621 | 8710 | 10331 | 464.941406
5600 | -2636 | 9785 | 12421 | 558.984375
5800 | -2597 | 10000 | 12597 | 566.894531
6000 | 2480 | 10000 | 7520 | 338.378906
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

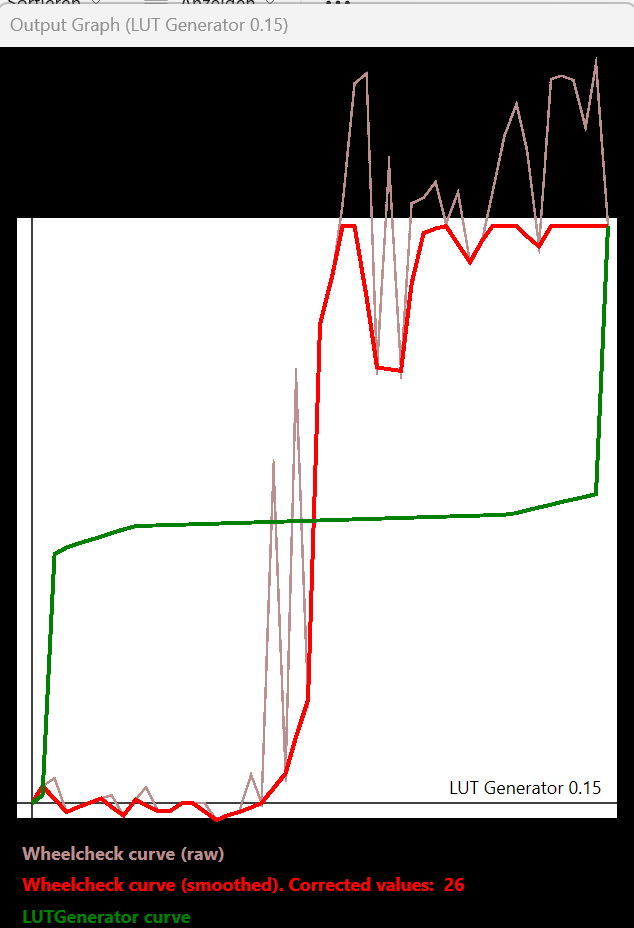
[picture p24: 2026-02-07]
docs/wheelcheck-step-log-2-original.png

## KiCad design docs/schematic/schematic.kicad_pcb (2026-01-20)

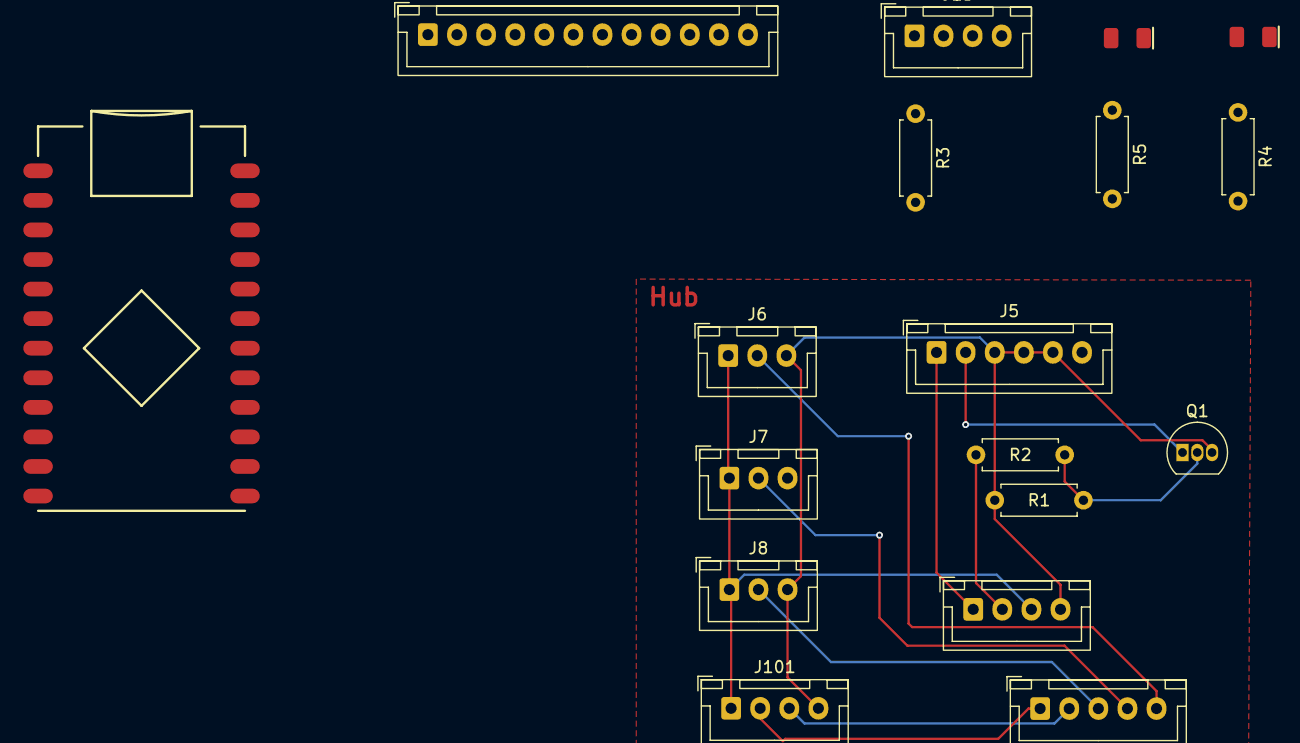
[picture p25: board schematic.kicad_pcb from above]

Board: 2 copper layers, 18 parts (0 on the bottom side), 25 nets.

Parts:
D2: Green; LED_1206_3216Metric_Red
D3: Blue; LED_1206_3216Metric_Blue
J1, J101: Analog Levers; JST_XH_B4B-XH-A_1x04_P2.50mm_Vertical
J2: JST_XH_B5B-XH-A_1x05_P2.50mm_Vertical
J5: Motor-PCB; JST_XH_B6B-XH-A_1x06_P2.50mm_Vertical
J6: X-Axis; JST_XH_B3B-XH-A_1x03_P2.50mm_Vertical
J7: Y-Axis; JST_XH_B3B-XH-A_1x03_P2.50mm_Vertical
J8: Z-Axis; JST_XH_B3B-XH-A_1x03_P2.50mm_Vertical
J12: Button Matrix; JST_XH_B12B-XH-A_1x12_P2.50mm_Vertical
J13: Front LED; JST_XH_B4B-XH-A_1x04_P2.50mm_Vertical
Q1: BC548; TO-92_Inline
R1, R4: 4.7k; R_Axial_DIN0207_L6.3mm_D2.5mm_P7.62mm_Horizontal
R2: 10k; R_Axial_DIN0207_L6.3mm_D2.5mm_P7.62mm_Horizontal
R3: 820; R_Axial_DIN0207_L6.3mm_D2.5mm_P7.62mm_Horizontal
R5: 150k; R_Axial_DIN0207_L6.3mm_D2.5mm_P7.62mm_Horizontal
U1: ProMicroC

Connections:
20V: J5.6, R5.2
/Motor_Enable: J5.2, Q1.1 (C)
/Motor_PWM: J1.1, J5.1, U1.12 (D9/A9)
GND: D2.1 (K), D3.1 (K), J1.4, J5.3, J5.4, J5.5, J6.3, J8.3, J13.2, J101.4, Q1.3 (E), R1.2, U1.3 (GND), U1.4 (GND), U1.23 (GND)
Matrix_Col1: J12.1, J12.9, U1.8 (D5)
Matrix_Col2: J12.2, J12.10, U1.15 (D14)
Matrix_Col3: J12.3, U1.16 (D15)
Matrix_Col4: J12.4, U1.5 (D2)
Matrix_Row1: J12.5, U1.9 (D6/A7)
Matrix_Row2: J12.6, J12.12, U1.10 (D7)
Matrix_Row3: J12.7, U1.11 (D8/A8)
Matrix_Row4: J12.8, U1.7 (D4/A6)
unnamed: D2.2 (A), R5.1
unnamed: D3.2 (A), R4.1
unnamed: J2.5, J6.2, U1.17 (A0)
unnamed: J2.4, J7.2, U1.18 (A1)
unnamed: J2.3, J8.2, U1.19 (A2)
unnamed: J13.1, R3.1
unnamed: J2.1, J101.2, U1.20 (A3)
unnamed: J2.2, J101.3, U1.13 (D10/A10)
unnamed: Q1.2 (B), R1.1, R2.2
unnamed: R3.2, U1.6 (D3)
unnamed: J1.2, R2.1, U1.14 (D16)
unnamed: R4.2, U1.2 (RX)
VCC: J1.3, J6.1, J7.1, J8.1, J101.1, U1.21 (5V)

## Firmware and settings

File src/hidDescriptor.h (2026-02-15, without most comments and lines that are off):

#pragma once
#include "ffb_hid.h"
#define USAGE_PAGE_GENERIC_DESKTOP 0x01
#define USAGE_PAGE_SIMULATION_CONTROLS 0x02
#define USAGE_GENERIC_X 0x30
#define USAGE_GENERIC_Y 0x31
#define USAGE_GENERIC_Z 0x32
#define USAGE_SIM_STEERING 0xC8
#define USAGE_SIM_BRAKE 0xC5
#define USAGE_SIM_ACCELERATOR 0xC4
#define USE_GENERIC_AXIS_DEFAULT_PROFILE
#define DEFAULT_USAGE_PAGE USAGE_PAGE_GENERIC_DESKTOP
#define DEFAULT_X_USAGE  USAGE_GENERIC_X
#define DEFAULT_Y_USAGE  USAGE_GENERIC_Y
#define DEFAULT_Z_USAGE  USAGE_GENERIC_Z
#define MAIN_AXES_USAGE_PAGE_OFFSET 11
#define AXES_X_USAGE_OFFSET (MAIN_AXES_USAGE_PAGE_OFFSET + 6)
#define AXES_Y_USAGE_OFFSET (AXES_X_USAGE_OFFSET + 14)
#define AXES_Z_USAGE_OFFSET (AXES_Y_USAGE_OFFSET + 4)
#define FFB_AXES_USAGE_PAGE_OFFSET (sizeof(_dynamicHidReportDescriptor) - 12 - NB_FF_AXIS * 2)
#define FFB_AXES_USAGE_OFFSET (FFB_AXES_USAGE_PAGE_OFFSET + 2)
#define INPUT_REPORT_ID 4
const uint8_t _dynamicHidReportDescriptor[] PROGMEM =
{
  0x05, 0x01,	// USAGE_PAGE (Generic Desktop)
  0x09, 0x04,	// USAGE (Joystick)
  0xA1, 0x01,	// COLLECTION (Application)
    0x85, INPUT_REPORT_ID,	// REPORT_ID (04)
    0xA1, 0x00, // COLLECTION (Physical)
      0x05, DEFAULT_USAGE_PAGE, // USAGE_PAGE (Generic Desktop: 0x01 / Simulation Controls: 0x02) [AXES_USAGE_PAGE_OFFSET]
      0x75, 0x10,            // REPORT_SIZE (16)
      0x95, 0x01,            // REPORT_COUNT (1)
      0x09, DEFAULT_X_USAGE, // USAGE (X / Steering) [AXES_X_USAGE_OFFSET]
      0x15, 0,               // LOGICAL_MINIMUM (X_AXIS_LOG_MIN = 0)
      0x26, 0xFF, 0x7F,      // LOGICAL_MAXIMUM (X_AXIS_LOG_MAX = 32767)
      0x81, 0x02,            // INPUT (Data,Var,Abs)
      0x15, 0,               // LOGICAL_MINIMUM (AXIS_LOG_MIN = 0)
      0x26, 0xFF, 0x03,      // LOGICAL_MAXIMUM (AXIS_LOG_MAX = 1023)
      0x09, DEFAULT_Y_USAGE, // USAGE (Y / Brake) [AXES_Y_USAGE_OFFSET]
      0x81, 0x02,            // INPUT (Data,Var,Abs)
      0x09, DEFAULT_Z_USAGE, // USAGE (Z / Accelerator) [AXES_Z_USAGE_OFFSET]
      0x81, 0x02,            // INPUT (Data,Var,Abs)
      0x05, 0x01,	           // USAGE_PAGE (Generic Desktop)
      0x09, 0x33,            // USAGE (rx)
      0x81, 0x02,            // INPUT (Data,Var,Abs)
      0x09, 0x34,            // USAGE (ry)
      0x81, 0x02,            // INPUT (Data,Var,Abs)
      0x09, 0x39,                     // USAGE (HAT SWITCH)
      0x15, 0x01,                     // LOGICAL_MINIMUM (1)
      0x25, 0x08,                     // LOGICAL_MAXIMUM (8)
      0x35, 0x00,                     // PHYSICAL_MINIMUM (0)
      0x46, 0x3B, 0x01,               // PHYSICAL_MAXIMUM (315)
      0x65, 0x14,                     // UNIT (Eng Rot:Angular Pos)
      0x55, 0x00,                     // UNIT_EXPONENT (0)
      0x75, 0x08,                     // REPORT_SIZE (8)
      0x95, 0x01,                     // REPORT_COUNT (1)
      0x81, 0x02,                     // Input (Data,Var,Abs)
      0x05, 0x09,                     // USAGE_PAGE (Button)
      0x15, 0x00,                     // LOGICAL_MINIMUM (0)
      0x25, 0x01,                     // LOGICAL_MAXIMUM (1)
      0x55, 0x00,                     // UNIT_EXPONENT (0)
      0x65, 0x00,                     // UNIT (None)
      0x19, 0x01,					            // USAGE_MINIMUM (button 1)
      0x29, NB_BUTTONS,               // USAGE_MAXIMUM (button NB_BUTTONS)
      0x75, 0x01,                     // REPORT_SIZE (1)
      0x95, NB_BUTTONS,               // REPORT_COUNT (number of buttons)
      0x81, 0x02,                     // Input (Data,Var,Abs)
      0x05, 0x01,                     // USAGE_PAGE (Generic Desktop)
      0x75, 0x01,                     // REPORT_SIZE (1)
      0x95, 8 - (NB_BUTTONS % 8),     // REPORT_COUNT (padding bits)
      0x81, 0x03,                     // Input (Const,Var,Abs)
    0xc0, // END_COLLECTION
    0x05, 0x0F,	// USAGE_PAGE (Physical Interface)
    0x09, 0x92,	// USAGE (PID State Report)
    0xA1, 0x02,	// COLLECTION (Logical)
      0x85, 0x02,	// REPORT_ID (02)
      0x09, 0x9F,	// USAGE (Device Paused)
      0x09, 0xA0,	// USAGE (Actuators Enabled)
      0x09, 0xA4,	// USAGE (Safety Switch)
      0x09, 0xA5,	// USAGE (Actuator Override Switch)
      0x09, 0xA6,	// USAGE (Actuator Power)
      0x15, 0x00,	// LOGICAL_MINIMUM (00)
      0x25, 0x01,	// LOGICAL_MINIMUM (01)
      0x35, 0x00,	// PHYSICAL_MINIMUM (00)
      0x45, 0x01,	// PHYSICAL_MAXIMUM (01)
      0x75, 0x01,	// REPORT_SIZE (01)
      0x95, 0x05,	// REPORT_COUNT (05)
      0x81, 0x02,	// INPUT (Data,Var,Abs)
      0x95, 0x03,	// REPORT_COUNT (03)
      0x81, 0x03,	// INPUT (Constant,Var,Abs)
      0x09, 0x94,	// USAGE (Effect Playing)
      0x15, 0x00,	// LOGICAL_MINIMUM (00)
      0x25, 0x01,	// LOGICAL_MAXIMUM (01)
      0x35, 0x00,	// PHYSICAL_MINIMUM (00)
      0x45, 0x01,	// PHYSICAL_MAXIMUM (01)
      0x75, 0x01,	// REPORT_SIZE (01)
      0x95, 0x01,	// REPORT_COUNT (01)
      0x81, 0x02,	// INPUT (Data,Var,Abs)
      0x09, 0x22,	// USAGE (Effect Block Index)
      0x15, 0x01,	// LOGICAL_MINIMUM (01)
      0x25, 0x28,	// LOGICAL_MAXIMUM (40)
      0x35, 0x01,	// PHYSICAL_MINIMUM (01)
      0x45, 0x28,	// PHYSICAL_MAXIMUM (40)
      0x75, 0x07,	// REPORT_SIZE (07)
      0x95, 0x01,	// REPORT_COUNT (01)
      0x81, 0x02,	// INPUT (Data,Var,Abs)
    0xC0,	// END COLLECTION ()
    0x09, 0x21,	// USAGE (Set Effect Output Report)
    0xA1, 0x02,	// COLLECTION (Logical)
      0x85, 0x01,	// REPORT_ID (01)
      0x09, 0x22,	// USAGE (Effect Block Index)
      0x15, 0x01,	// LOGICAL_MINIMUM (01)
      0x25, 0x28,	// LOGICAL_MAXIMUM (40)
      0x35, 0x01,	// PHYSICAL_MINIMUM (01)
      0x45, 0x28,	// PHYSICAL_MAXIMUM (40)
      0x75, 0x08,	// REPORT_SIZE (08)
      0x95, 0x01,	// REPORT_COUNT (01)
      0x91, 0x02,	// OUTPUT (Data,Var,Abs)
      0x09, 0x25,	// USAGE (Effect type)
      0xA1, 0x02,	// COLLECTION (Logical)
        0x09, 0x26,	// USAGE (ET Constant Force)
        0x09, 0x27,	// USAGE (ET Ramp)
        0x09, 0x30,	// USAGE (ET Square)
        0x09, 0x31,	// USAGE (ET Sine)
        0x09, 0x32,	// USAGE (ET Triangle)
        0x09, 0x33,	// USAGE (ET Sawtooth Up)
        0x09, 0x34,	// USAGE (ET Sawtooth Down)
        0x09, 0x40,	// USAGE (ET Spring)
        0x09, 0x41,	// USAGE (ET Damper)
        0x09, 0x42,	// USAGE (ET Inertia)
        0x09, 0x43,	// USAGE (ET Friction)
        0x25, 0x0B,  // LOGICAL_MAXIMUM (11) //milos, 1 less effect
        0x15, 0x01,	// LOGICAL_MINIMUM (01)
        0x35, 0x01,	// PHYSICAL_MINIMUM (01)
        0x45, 0x0B,  // PHYSICAL_MAXIMUM (11) //milos, 1 less effect
        0x75, 0x08,	// REPORT_SIZE (08)
        0x95, 0x01,	// REPORT_COUNT (01)
        0x91, 0x00,	// OUTPUT (Data)
      0xC0,	// END COLLECTION ()
      0x09, 0x50,	// USAGE (Duration)
      0x09, 0x54,	// USAGE (Trigger Repeat Interval)
      0x15, 0x00,	// LOGICAL_MINIMUM (00)
      0x27, 0xFF, 0xFF, 0x00, 0x00,	// LOGICAL_MAXIMUM (65535)
      0x35, 0x00,	// PHYSICAL_MINIMUM (00)
      0x47, 0xFF, 0xFF, 0x00, 0x00,	// PHYSICAL_MAXIMUM (65535)
      0x66, 0x01, 0x10,  // UNIT (SI Lin:Time)
      0x55, 0xFD,  // UNIT_EXPONENT (-3)
      0x75, 0x10,	// REPORT_SIZE (16)
      0x95, 0x02,  // REPORT_COUNT (02) //milos
      0x91, 0x02,	// OUTPUT (Data,Var,Abs)
      0x55, 0x00,	// UNIT_EXPONENT (00)
      0x66, 0x00, 0x00,	// UNIT (None)
      0x09, 0x52,	// USAGE (Gain)
      0x15, 0x00,	// LOGICAL_MINIMUM (00)
      0x26, 0xFF, 0x7F, // LOGICAL_MAXIMUM (32767) //milos
      0x35, 0x00,	// PHYSICAL_MINIMUM (00)
      0x46, 0xFF, 0x7F,  // PHYSICAL_MAXIMUM (32767) //milos
      0x75, 0x10,  // REPORT_SIZE (16) //milos
      0x95, 0x01,	// REPORT_COUNT (01)
      0x91, 0x02,	// OUTPUT (Data,Var,Abs)
      0x09, 0x53,	// USAGE (Trigger Button)
      0x15, 0x01,	// LOGICAL_MINIMUM (01)
      0x25, 0x08,	// LOGICAL_MAXIMUM (08)
      0x35, 0x01,	// PHYSICAL_MINIMUM (01)
      0x45, 0x08,	// PHYSICAL_MAXIMUM (08)
      0x75, 0x08,	// REPORT_SIZE (08)
      0x95, 0x01,	// REPORT_COUNT (01)
      0x91, 0x02,	// OUTPUT (Data,Var,Abs)
      0x09, 0x55,	// USAGE (Axes Enable)
      0xA1, 0x02,	// COLLECTION (Logical)
        0x05, DEFAULT_USAGE_PAGE, // USAGE_PAGE (Generic Desktop: 0x01 / Simulation Controls: 0x02) [FFB_AXES_USAGE_PAGE_OFFSET]
        0x09, DEFAULT_X_USAGE, // USAGE (X / Steering) [FFB_AXES_USAGE_OFFSET]
        #if (NB_FF_AXIS > 1)
          0x09, 0x31,	// USAGE (Y)
        #endif
        0x15, 0x00,	// LOGICAL_MINIMUM (00)
        0x25, 0x01,	// LOGICAL_MAXIMUM (01)
        0x75, 0x01,	// REPORT_SIZE (01)
        0x95, NB_FF_AXIS,	// REPORT_COUNT (NB_FF_AXIS)
        0x91, 0x02,	// OUTPUT (Data,Var,Abs)
      0xC0,	// END COLLECTION () // "Set Effect Output Report" continued in _staticHidReportDescriptor ...
};
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

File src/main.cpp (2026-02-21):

/* Arduino Leonardo Force Feedback Wheel firmware

  Copyright 2015  Etienne Saint-Paul  (esaintpaul [at] gameseed [dot] fr)
  Copyright 2017  Fernando Igor  (fernandoigor [at] msn [dot] com)
  Copyright 2018-2025  Milos Rankovic (ranenbg [at] gmail [dot] com)

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
  The author disclaim all warranties with regard to this
  software, including all implied warranties of merchantability
  and fitness.  In no event shall the author be liable for any
  special, indirect or consequential damages or any damages
  whatsoever resulting from loss of use, data or profits, whether
  in an action of contract, negligence or other tortious action,
  arising out of or in connection with the use or performance of
  this software.
*/

#include <Arduino.h>

#include "config.h"
#include "ffb_hid.h"
#include "ffb_pro.h"
#include "hidDescriptor.h"
#include "common.h"
#include "debug.h"
#include "packed.h"

s16a accel;
s16a clutch;
s16a hbrake;
s16a brake;

cFFB gFFB;

HidAdapter hidAdapter;

bool useCombinedAxes = false;


static void updateFfb();
static void createAndSendInputReport();
static void sendInputReport(int16_t x, int16_t y, int16_t z, int16_t rx, int16_t ry, uint8_t hat, uint16_t buttons);
static void updateDataLed();

void initLeds() {
  pinMode(LED_BLUE_PIN, OUTPUT);
  digitalWrite(LED_BLUE_PIN, LOW);

  pinMode(FFBCLIP_LED_PIN, OUTPUT);
  digitalWrite(FFBCLIP_LED_PIN, LOW);
}

void setup() {
  initLeds();

  CONFIG_SERIAL.begin(115200);

  initInputs();
  hidAdapter.begin();

  accel.val = 0;
  brake.val = 0;
  clutch.val = 0;

  initEEPROMConfig();
  setEEPROMConfig(); // check firmware version from EEPROM (if any) and load defaults if required
  loadEEPROMConfig(); // read firmware setings from EEPROM and update current firmware settings

  FfbSetDriver(0);

  initPWM(); // initialize PWM (or DAC) settings
  setPWM(0); // zero PWM at startup

  blinkFfbClipLED(); // this blocks for some ms. Do it last
}

void loop() {
  static uint32_t lastRefreshTimeUs = 0;
  static uint32_t lastConfigSerialUpdateTimeUs = 0;

  readAxesSamples();

  uint32_t nowUs = micros();
  if ((nowUs - lastRefreshTimeUs >= CONTROL_PERIOD_US) && hidAdapter.isReady()) {
    updateFfb();
    createAndSendInputReport();
    lastRefreshTimeUs += CONTROL_PERIOD_US;
  }

  if (nowUs - lastConfigSerialUpdateTimeUs >= CONFIG_SERIAL_PERIOD_US) {
    configCDC(); // configure firmware with virtual serial port
    lastConfigSerialUpdateTimeUs = nowUs;
  }

  updateDataLed();

  hidAdapter.recvFromUsb();
}

#define FFB_AXIS_RAW_BITS 15 // raw read value resolution before scaling to range of FFB lib
#define FFB_AXIS_RAW_MAX_VALUE ((1L << FFB_AXIS_RAW_BITS) - 1) // raw read max value before scaling to range of FFB lib

static void updateFfb() {
  int16_t ffbAxisValueRaw = getAxisValue(AXIS_ID_X, FFB_AXIS_RAW_BITS, AVG_FFB_AXIS_X_NUM_MAX_SAMPLES); // only use the newest samples for averaging of FFB axis to reduce latency
  s32v ffbAxisValue; // position input for calculating ffb
  ffbAxisValue.x = map(ffbAxisValueRaw, 0, FFB_AXIS_RAW_MAX_VALUE, -FFB_ROTATION_MID - 1, FFB_ROTATION_MID);

  s32v ffbs = gFFB.CalcTorqueCommands(&ffbAxisValue); // raw units -inf,0,inf
  setPWM(ffbs.x);
  updateFfbClipLED(ffbs.x);
}

static void createAndSendInputReport() {
  int16_t turnXRaw = getAxisValue(AXIS_ID_X, X_AXIS_NB_BITS, AVG_AXIS_NUM_MAX_SAMPLES); // get averaged X axis for all samples for smoother USB report
  int16_t deadZoneX = (X_AXIS_LOG_MAX - (X_AXIS_LOG_MAX * ROTATION_DEG / FFB_ROTATION_DEG)) / 2;
  int32_t turnX = map(turnXRaw, 0, X_AXIS_LOG_MAX, deadZoneX, X_AXIS_LOG_MAX - deadZoneX);
  turnX = constrain(turnX, 0, X_AXIS_LOG_MAX);

  bool pedalsConnected = checkPedalsConnected(
    getAxisValue(AXIS_ID_Y, 8, 1),
    getAxisValue(AXIS_ID_Z, 8, 1));

  if (pedalsConnected) { // pedals attached, use levers as additional axes
    accel.val = getAxisValue(AXIS_ID_Z, Z_AXIS_NB_BITS, AVG_AXIS_NUM_MAX_SAMPLES);
    brake.val = getAxisValue(AXIS_ID_Y, Y_AXIS_NB_BITS, AVG_AXIS_NUM_MAX_SAMPLES);
    clutch.val = getAxisValue(AXIS_ID_RX, RX_AXIS_NB_BITS, AVG_AXIS_NUM_MAX_SAMPLES);
    hbrake.val = getAxisValue(AXIS_ID_RY, RY_AXIS_NB_BITS, AVG_AXIS_NUM_MAX_SAMPLES);
  } else { // no pedals attached, use levers as accel and brake
    accel.val = getAxisValue(AXIS_ID_RY, Z_AXIS_NB_BITS, AVG_AXIS_NUM_MAX_SAMPLES);
    brake.val = getAxisValue(AXIS_ID_RX, Y_AXIS_NB_BITS, AVG_AXIS_NUM_MAX_SAMPLES);
    clutch.val = 0; // RX axis
    hbrake.val = 0; // RY axis
  }

  if (useCombinedAxes) {
    if (accel.val > brake.val) {
      brake.val = (Y_AXIS_LOG_MAX + accel.val) / 2;
    } else {
      brake.val = (Y_AXIS_LOG_MAX - brake.val) / 2;
    }
    accel.val = 0;
  }

  // rescale all analog axis according to manual calibration
  brake.val = map(brake.val, brake.min, brake.max, 0, Y_AXIS_LOG_MAX);
  brake.val = constrain(brake.val, 0, Y_AXIS_LOG_MAX);

  accel.val = map(accel.val, accel.min, accel.max, 0, Z_AXIS_LOG_MAX);
  accel.val = constrain(accel.val, 0, Z_AXIS_LOG_MAX);

  clutch.val = map(clutch.val, clutch.min, clutch.max, 0, RX_AXIS_LOG_MAX);
  clutch.val = constrain(clutch.val, 0, RX_AXIS_LOG_MAX);

  hbrake.val = map(hbrake.val, hbrake.min, hbrake.max, 0, RY_AXIS_LOG_MAX);
  hbrake.val = constrain(hbrake.val, 0, RY_AXIS_LOG_MAX);

  
  uint16_t buttonsRaw = readInputButtonsRaw();
  uint8_t hat = decodeHatSwitch(buttonsRaw & 0b1111); // only take first 4 bits from raw input buttons
  uint16_t buttons = buttonsRaw >>= 4; // shift out the hat bits from buttons variable

  sendInputReport(turnX, brake.val, accel.val, clutch.val, hbrake.val, hat, buttons);
}

#define SWAP_BITS(bits) ((((bits) << 1) & 0x2) | (((bits) >> 1) & 0x1))

static uint16_t rearrangeButtons(uint16_t buttons) {
  uint8_t gearBtns = buttons & 0b11;
  uint8_t dpadBtns = (buttons >> 2) & 0b1111;
  uint8_t sideBtns = SWAP_BITS((buttons >> 8) & 0b11);
  uint16_t frontButtons = SWAP_BITS((buttons >> 10) & 0b11);
  return dpadBtns | (frontButtons << 4) | (sideBtns << 6) | (gearBtns << 8);
}

struct ATTR_PACKED InputReport {
  int16_t x;
  int16_t y;
  int16_t z;
  int16_t rx;
  int16_t ry;
  uint8_t hat;
  uint16_t buttons : NB_BUTTONS;
  uint8_t padding : 8 - (NB_BUTTONS % 8);
};

static void sendInputReport(int16_t x, int16_t y, int16_t z, int16_t rx, int16_t ry, uint8_t hat, uint16_t buttons) {
  InputReport report = {
    x: x,
    y: y,
    z: z,
    rx: rx,
    ry: ry,
    hat: hat,
    buttons: rearrangeButtons(buttons)
  };
  hidAdapter.sendInputReport(INPUT_REPORT_ID, (uint8_t*)&report, sizeof(report));
}

/**
 * Blinks the FFB clip LED a few times at startup to indicate succesful boot.
 * Note: this blocks for some ms. Only use at start-up.
 */ 
void blinkFfbClipLED() {
  const uint8_t blinkCount = 3;
  for (uint8_t i = 0; i < blinkCount; i++) {
    if (i > 0) {
      delay(200);
    }
    digitalWrite(FFBCLIP_LED_PIN, HIGH);
    delay(200);
    digitalWrite(FFBCLIP_LED_PIN, LOW);
  }
}

constexpr uint16_t HIGH_TORQUE_PWM_MAX = FFBCLIP_LED_MAX_VALUE * 63 / 255;

/**
 * Turns the FFB clip LED on if max FFB signal reached.
 * Shows 90-99% of FFB signal as linear increase from 0 to 1/4 of full brightness.
 */
void updateFfbClipLED(int32_t torque) {
  static int16_t oldPwmValue = -1;

  const float gainPercent = configGeneralGain / 100.f;
  const int32_t maxTorque = gainPercent * MM_MAX_MOTOR_TORQUE;
  const int32_t highTorque = 0.9f * maxTorque;

  int16_t pwmValue;
  if (abs(torque) >= highTorque && abs(torque) < maxTorque - 1) {
    pwmValue = map(abs(torque), highTorque, maxTorque, 1, HIGH_TORQUE_PWM_MAX); // for 90%-99% ffb map brightness linearly from 1-63 (out of 255)
  } else if (abs(torque) >= maxTorque - 1) {
    pwmValue = FFBCLIP_LED_MAX_VALUE; // for 100% FFB set full brightness
  } else {
    pwmValue = 0; // if under 90% FFB turn off LED
  }

  if (oldPwmValue != pwmValue) {
    analogWrite(FFBCLIP_LED_PIN, pwmValue);
    oldPwmValue = pwmValue;
  }
}

static void updateDataLed() {
  if (dataLedActiveTimeMs > 0 && millis() - dataLedActiveTimeMs > 1) {
    digitalWrite(LED_BLUE_PIN, LOW);
    dataLedActiveTimeMs = 0;
  }
}

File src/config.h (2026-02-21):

#pragma once

#include <stdint.h>

//------------------------------------- Firmware options -------------------------------------------------

#define USE_PWM_0_50_100_MODE
//#define USE_PWM_DIR_MODE
//#define USE_PWM_PLUS_MINUS_MODE

#define MOTOR_PWM_BITS 11
#define MOTOR_PWM_MAX_VALUE ((1L << MOTOR_PWM_BITS) - 1) // 2047
#define MAX_TORQUE_DEFAULT MOTOR_PWM_MAX_VALUE

//------------------------------------- Pins -------------------------------------------------------------

// Note: Green LED directly connected to +12V supply, not controllable
#ifdef __AVR__
#define LED_BLUE_PIN 0
#define LED_RED_PIN 3 // connected to TIMER0B (8-bit) for PWM
#define FFBCLIP_LED_PIN LED_RED_PIN
#define FFBCLIP_LED_MAX_VALUE 255 // LED has timer separate from motor PWM
#else
#define LED_BLUE_PIN 39
#define LED_RED_PIN 40
#define FFBCLIP_LED_PIN LED_RED_PIN
#define FFBCLIP_LED_MAX_VALUE MOTOR_PWM_MAX_VALUE // LED shares precision with motor PWM (limitation in Arduino implementation)
#endif

#ifdef __AVR__
#define X_AXIS_PIN		A0
#define Y_AXIS_PIN    A1
#define Z_AXIS_PIN		A2
#define RX_AXIS_PIN		A3
#define RY_AXIS_PIN   A8
#else
#define X_AXIS_PIN		A0
#define Y_AXIS_PIN    A1
#define Z_AXIS_PIN		A3
#define RX_AXIS_PIN		A4
#define RY_AXIS_PIN   A5
#endif

#ifdef __AVR__
#define BUTTON_MATRIX_COL0_PIN 5
#define BMCOL0_PORTBIT 6
#define BUTTON_MATRIX_COL1_PIN 14
#define BMCOL1_PORTBIT 3
#define BUTTON_MATRIX_COL2_PIN 15
#define BMCOL2_PORTBIT 1
#define BUTTON_MATRIX_COL3_PIN 2
#define BMCOL3_PORTBIT 1

#define BUTTON_MATRIX_ROW0_PIN 4
#define BUTTON_MATRIX_ROW1_PIN 7
#define BUTTON_MATRIX_ROW2_PIN 1
#define BUTTON_MATRIX_ROW3_PIN 6
#else
#define BUTTON_MATRIX_COL0_PIN 38
#define BUTTON_MATRIX_COL1_PIN 37
#define BUTTON_MATRIX_COL2_PIN 36
#define BUTTON_MATRIX_COL3_PIN 35

#define BUTTON_MATRIX_ROW0_PIN 34 //?
#define BUTTON_MATRIX_ROW1_PIN 33 //?
#define BUTTON_MATRIX_ROW2_PIN 18 //?
#define BUTTON_MATRIX_ROW3_PIN 17 //?
#endif

#define PROFILE_SWITCH_PIN 7

#ifdef __AVR__
#define PWM_PIN_L     9 // left PWM pin
#if defined(USE_PWM_0_50_100_MODE) || defined(USE_PWM_DIR_MODE)
#define DIR_PIN       10
#else
#define PWM_PIN_R     10 // right PWM pin
#endif
#else
#define PWM_PIN_L     42 // left PWM pin
#if defined(USE_PWM_0_50_100_MODE) || defined(USE_PWM_DIR_MODE)
#define DIR_PIN       41
#else
#define PWM_PIN_R     41 // right PWM pin
#endif
#endif

//------------------------------------- EEPROM Config -----------------------------------------------------

#define PARAM_ADDR_FW_VERSION		 0x00 // firmware version
#define PARAM_ADDR_ENC_OFFSET    0x02 // Z-index offset
#define PARAM_ADDR_ROTATION_DEG  0x06 // rotation degrees
#define PARAM_ADDR_GEN_GAIN      0x08 // general
#define PARAM_ADDR_DMP_GAIN      0x09 // damper
#define PARAM_ADDR_FRC_GAIN      0x0A // friction
#define PARAM_ADDR_CNT_GAIN      0x0B // constant
#define PARAM_ADDR_PER_GAIN      0x0C // periodic
#define PARAM_ADDR_SPR_GAIN      0x0D // spring
#define PARAM_ADDR_INR_GAIN      0x0E // inertia
#define PARAM_ADDR_CTS_GAIN      0x0F // centering spring
#define PARAM_ADDR_STP_GAIN      0x10 // end stop
#define PARAM_ADDR_MIN_TORQ      0x11 // min torque
#define PARAM_ADDR_MAX_TORQ      0x13 // max torque
#define PARAM_ADDR_MAX_DAC       0x15 // max DAC value
#define PARAM_ADDR_BRK_PRES      0x17 // max brake pressure
#define PARAM_ADDR_DSK_EFFC      0x18 // desktop effects (byte contents is in effstate)
#define PARAM_ADDR_ENC_CPR       0x19 // encoder CPR
#define PARAM_ADDR_PWM_SET       0x1D // PWM settings and frequency (byte contents is in pwmstate)
#define PARAM_ADDR_SHFT_X0       0x1E // XY shifter limit x0
#define PARAM_ADDR_SHFT_X1       0x20 // XY shifter limit x1
#define PARAM_ADDR_SHFT_X2       0x22 // XY shifter limit x2
#define PARAM_ADDR_SHFT_Y0       0x24 // XY shifter limit y0
#define PARAM_ADDR_SHFT_Y1       0x26 // XY shifter limit y1
#define PARAM_ADDR_SHFT_CFG      0x28 // shifter configuration byte
#define PARAM_ADDR_ACEL_LO       0x2A // accelerator pedal cal min
#define PARAM_ADDR_ACEL_HI       0x2C // accelerator pedal cal max
#define PARAM_ADDR_BRAK_LO       0x2E // brake pedal cal min
#define PARAM_ADDR_BRAK_HI       0x30 // brake pedal cal max
#define PARAM_ADDR_CLUT_LO       0x32 // clutch pedal cal min
#define PARAM_ADDR_CLUT_HI       0x34 // clutch pedal cal max
#define PARAM_ADDR_HBRK_LO       0x36 // hand brake pedal cal min
#define PARAM_ADDR_HBRK_HI       0x38 // hand brake pedal cal max

#define EEPROM_SIZE              1024 // same as used for Arduino Pro Micro

#define FIRMWARE_VERSION         0x01 //  firmware version

void setParam (uint16_t offset, uint8_t *addr_to, uint8_t size);

#define GetParam(m_offset,m_data)	getParam((m_offset),(uint8_t*)&(m_data),sizeof(m_data))
#define SetParam(m_offset,m_data)	setParam((m_offset),(uint8_t*)&(m_data),sizeof(m_data))

//------------------------------------- Main Config -----------------------------------------------------
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

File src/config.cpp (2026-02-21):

#include <Arduino.h>
#include <EEPROM.h>
#include "config.h"
#include "common.h"

uint8_t ffbBalance; // load cell scaling factor (affects brake pressure, but depends on your load cell's maximum specified load)

// these are now loaded from EEPROM
uint8_t effstate; // = 0b00000001; // turn on/off desktop effects through serial interface, bit 7 is MSB

//---------------------
// bit0-phase correct (0 is fast pwm), bit1-dir enabled (0 is pwm+-), bits 2-5 are frequency select, bit6-enable pwm0-50-100, bit7 is unused
// bit0 pwm_type
// 0    fast pwm
// 1    phase correct

// bits2-5 define frequency index, bit2 is MSB, see firmware_info.txt for details

// bit1 bit6 pwm_mode
// 0    0    pwm+-
// 0    1    pwm0-50-100
// 1    0    pwm+dir
// 1    1    rcm
//----------------------

// if USE_MCP4725 is defined then pwmstate byte has the following interpretation
//----------------
// bits 0-4 unused, bit5-enable dac0-50-100, bit6-enable dac+dir (0 is dac+-), bit7-enable dac (0 is zero dac output)

// bit7 dac_out
// 0   disabled (set to 0V or 2.5V depending on dac mode)
// 1   enabled

// bit6 bit5 dac_mode      dac_mode2 (2-ffb axis)
// 0    0    dac+-         1ch dac+- (xFFB)
// 0    1    dac0-50-100   2ch dac0-50-100
// 1    0    dac+dir       2ch dac+dir
// 1    1    none
//----------------
uint8_t pwmstate; // PWM settings configuration byte, bit7 is MSB

// changed these from float to uint8_t (loaded from EEPROM)
uint8_t configGeneralGain;  // = 100;
uint8_t configDamperGain; // = 1.0f;		// was 0.5f
uint8_t configFrictionGain; // = 1.0f;	// was 0.5f
uint8_t configConstantGain; // = 1.0f;
uint8_t configPeriodicGain; // = 1.0f;
uint8_t configSpringGain; // = 1.0f
uint8_t configInertiaGain; // = 1.0f
uint8_t configCenterGain; // = 0.7f
uint8_t configStopGain; // = 1.0f


uint16_t PWMtops [13] =
{
  400,  // 0
  800,  // 1
  1023, // 2
  2047, // 3
  4095, // 4
  5000, // 5
  10000, // 6
  16383, // 7
  20000, // 8
  32767, // 9
  30000, // 10
  40000, // 11
  65535  // 12
};

int16_t ROTATION_DEG;
int32_t CPR; // counts-per-rotation. Unused, as this only makes sense for optical or magnetic encoders
uint16_t MM_MIN_MOTOR_TORQUE; // loaded from EEPROM
uint16_t MM_MAX_MOTOR_TORQUE; // loaded from EEPROM
uint16_t MAX_DAC; // loaded from EEPROM

//-------------------------------------------------------------------------------------------------------

void getParam (uint16_t offset, uint8_t *addr_to, uint8_t size) {
  for (uint8_t i = 0; i < size; i++) {
    addr_to[i] = EEPROM.read(offset + i);
  }
}

void setParam (uint16_t offset, uint8_t *addr_to, uint8_t size) {
  for (uint8_t i = 0; i < size; i++) {
  #ifdef __AVR__
    EEPROM.update(offset + i, addr_to[i]); //re-write only when neccessary
  #else
    EEPROM.write(offset + i, addr_to[i]);
  #endif
  }
}

void initEEPROMConfig() {
#ifndef __AVR__
  EEPROM.begin(EEPROM_SIZE);
#endif
}

void SetDefaultEEPROMConfig() { // store default firmware settings in EEPROM
  uint16_t v16;
  int32_t v32;
  uint8_t v8;
  v16 = FIRMWARE_VERSION;
  SetParam(PARAM_ADDR_FW_VERSION, v16);
  v32 = 0;
  SetParam(PARAM_ADDR_ENC_OFFSET, v32);
  v16 = 1080; //default degrees of rotation. Although we only have 210°, 1080° seem to result in better force feedback behavior
  SetParam(PARAM_ADDR_ROTATION_DEG, v16);
  v8 = 100;
  SetParam(PARAM_ADDR_GEN_GAIN, v8);
  SetParam(PARAM_ADDR_CNT_GAIN, v8);
  SetParam(PARAM_ADDR_PER_GAIN, v8);
  SetParam(PARAM_ADDR_STP_GAIN, v8);
  SetParam(PARAM_ADDR_SPR_GAIN, v8);
  v8 = 50;
  SetParam(PARAM_ADDR_DMP_GAIN, v8);
  SetParam(PARAM_ADDR_FRC_GAIN, v8);
  SetParam(PARAM_ADDR_INR_GAIN, v8);
  v8 = 70;
  SetParam(PARAM_ADDR_CTS_GAIN, v8);
  v16 = 0;
  SetParam(PARAM_ADDR_MIN_TORQ, v16);
  v16 = MAX_TORQUE_DEFAULT; // for PWM signals
  SetParam(PARAM_ADDR_MAX_TORQ, v16);
  v16 = 4095; // for 12bit DAC
  SetParam(PARAM_ADDR_MAX_DAC, v16);
  v8 = 128; // ffb balance center value
  SetParam(PARAM_ADDR_BRK_PRES, v8);
  v8 = 0b00000001; // autocenter spring on
  SetParam(PARAM_ADDR_DSK_EFFC, v8);
  v32 = 2400; // default CPR value for optical encoder (this is for 600PPR)
  SetParam(PARAM_ADDR_ENC_CPR, v32);
  v8 = 0b01000100; // PWM out enabled, fast pwm, pwm+-, 7.8kHz, TOP 11bit (2047)
  SetParam(PARAM_ADDR_PWM_SET, v8);
  v16 = 0;
  SetParam(PARAM_ADDR_ACEL_LO, v16);
  SetParam(PARAM_ADDR_BRAK_LO, v16);
  SetParam(PARAM_ADDR_CLUT_LO, v16);
  SetParam(PARAM_ADDR_HBRK_LO, v16);
  v16 = 1023;
  SetParam(PARAM_ADDR_ACEL_HI, v16);
  SetParam(PARAM_ADDR_BRAK_HI, v16);
  SetParam(PARAM_ADDR_CLUT_HI, v16);
  SetParam(PARAM_ADDR_HBRK_HI, v16);
#ifndef __AVR__
  EEPROM.commit();
#endif
}

void setEEPROMConfig() { // changed FIRMWARE_VERSION to 16bit from 32bit
  uint16_t v16;
  GetParam(PARAM_ADDR_FW_VERSION, v16);
  if (v16 != FIRMWARE_VERSION) { // first time run, or version change - set default values for safety
    SetDefaultEEPROMConfig(); // set default firmware settings
  }
}
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

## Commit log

2026-01-04 config and modify for Guillemot wheel
2026-01-07 update data LED
2026-01-07 add motor switch ltspice simulation
2026-01-07 fix motor enable switch
2026-01-20 fix JP101 pin order
2026-01-20 add schematic
    [motor.kicad_sch, schematic.kicad_pcb, schematic.kicad_sch]
2026-01-20 switch brake and accelerator axes
2026-01-24 hardcode pwm mode
2026-01-24 update motor schema
    [motor.kicad_sch]
2026-01-24 update wiring
    [schematic.kicad_sch]
2026-01-25 de-jitter x-axis
2026-01-25 update schematic
    [schematic.kicad_sch]
2026-01-25 update to AVR Arduino 1.8.7 framework
2026-01-31 remove unused files
    [Firmware-v24X button mappings.xlsx]
2026-01-31 detect pedal removal
    [schematic.kicad_sch]
2026-02-01 fix force feedback for steering wheel profile
    [hidDescriptor.h]
2026-02-02 add profile switch
    [schematic.kicad_sch]
2026-02-03 fix offsets for steering mode
    [hidDescriptor.h]
2026-02-04 replace running average with normal average for better feedback
    [brWheel_my.cpp]
2026-02-05 add x-axis scaling
2026-02-07 add force diagram
    [wheelcheck-step-log-2-original.csv]
2026-02-09 support for esp32
2026-02-15 add pwm support for ESP32
2026-02-15 fix pwm
2026-02-17 fix axis and profile switch
    [ffb_hid.cpp, ffb_pro.cpp, main.cpp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]
2026-02-17 fix buttons
2026-02-17 set usb device name
2026-02-18 fix input matrix init
    [inputs.cpp]
2026-02-21 improve latency for ESP32
2026-02-21 fix FFB Clip LED
    [config.cpp, config.h, main.cpp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]
2026-02-21 adjust sampleing requency
2026-02-21 add profile for wheel control program

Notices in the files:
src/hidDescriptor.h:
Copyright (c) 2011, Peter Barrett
